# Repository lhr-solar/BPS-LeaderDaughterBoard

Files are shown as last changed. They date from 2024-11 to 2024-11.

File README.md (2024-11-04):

# BPS-LeaderDaughterBoard

The BPS Leader-Daughter is a daugherboard for the LeaderSOM. Together they will read data from and control the BPS peripherals

## Switches LEDs
| # | Purpose |
| - | - |
| D1  | Strobe Light Indicator |
| D3  | HV+ Contactor Indicator |
| D6  | HV- Contactor Indicator |
| D9  | Array Contactor Indicator |

[**BOM**](BOM/BPS-LeaderDaughterBOM.xls)  
[**IBOM**](BOM/ibom.html)  
[**Partial Mouser Cart**](https://www.mouser.com/ProjectManager/ProjectDetail.aspx?AccessID=2f994263ce7)  
[**All Components Mouser Cart**](https://www.mouser.com/ProjectManager/ProjectDetail.aspx?AccessID=f3b4372aef)  

## PCB


## Schematic
[**PDF with all sheets**](BPS-LeaderDaughterSchematic.pdf)

## Links
[Gigavac Contactor Circuit PWM Application Note](https://sensata.com/sites/default/files/a/Sensata-gigavac-driving-contactors-with-external-pwm-app-note.pdf)  
[Texas Instruments note on driving Contactors](https://www.ti.com/lit/wp/slvaf35/slvaf35.pdf?ts=1699022514322&ref_url=https%253A%252F%252Fwww.google.com%252F)

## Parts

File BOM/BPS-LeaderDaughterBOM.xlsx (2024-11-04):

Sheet: Full BOM
Reference | Value | Footprint | P/N | Qty
C1 | 1uF | Capacitor_SMD:C_0805_2012Metric | C0805C105K5PACTU | 1
D1, D3, D6, D9 | Green | LED_SMD:LED_0805_2012Metric_Pad1.15x1.40mm_HandSolder | APTD2012LCGCK | 4
D2, D5, D8 | BAS70-04 | Package_TO_SOT_SMD:SOT-23 | BAS70-04 | 3
D4, D7, D10, D11, D13, D15, D17 | 1N4448W | Diode_SMD:D_SOD-123 | 1N4448W | 7
D12, D14, D16, D18 | 3.3V | Diode_SMD:D_SOD-323 | BZT52B3V3 | 4
IC1 | ADT7470ARQZ-REEL7 | Package_SO:QSOP-16_3.9x4.9mm_P0.635mm | ADT7470 | 1
J1, J2 | DaughterConnector | UTSVT_Connectors:Molex_53307-2071 | 53307-2071 | 2
J3 | ErrorLightConn | UTSVT_Connectors:Molex_MicroFit3.0_1x2xP3.00mm_PolarizingPeg_Vertical | 43650-0215 | 1
J4-J7, J9-J12 | Conn_01x04 | UTSVT_Connectors:Molex_MicroFit3.0_1x4xP3.00mm_PolarizingPeg_Vertical | 436500244 | 8
J8 | Conn_01x03 | Connector_Molex:Molex_Micro-Fit_3.0_43650-0315_1x03_P3.00mm_Vertical | 436500315 | 1
Q1-Q8 | BUK9M23-80E | Package_TO_SOT_SMD:LFPAK33 | BUK9M23-80E | 8
R1, R5, R9, R13 | 1k | Resistor_SMD:R_0805_2012Metric | CRCW08051K00FKEAC | 4
R2, R7, R11, R15, R22, R24, R27, R29, R32, R34, R37, R39 | 10k | Resistor_SMD:R_0805_2012Metric | CRCW080510K0FKEAC | 12
R3, R6, R10, R14, R16, R18, R20, R21, R25, R26, R30, R31, R35, R36 | 100k | Resistor_SMD:R_0805_2012Metric | CRCW0805100KFKEAC | 14
R17, R19 | 600 | Resistor_SMD:R_0805_2012Metric | CRCW0805600RFKEAHP | 2
R23, R28, R33, R38 | 20k | Resistor_SMD:R_0805_2012Metric | CRCW080522K1FKEA | 4
U1, U2 | EL3H7 | Package_SO:SOP-4_4.4x2.6mm_P1.27mm | EL3H7(D)(TA)-VG | 2

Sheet: BOM to Order
Reference | Value | Footprint | P/N | Qty
D2, D5, D8 | BAS70-04 | Package_TO_SOT_SMD:SOT-23 | BAS70-04 | 3
D4, D7, D10, D11, D13, D15, D17 | 1N4448W | Diode_SMD:D_SOD-123 | 1N4448W | 7
D12, D14, D16, D18 | 3.3V | Diode_SMD:D_SOD-323 | BZT52B3V3 | 4
IC1 | ADT7470ARQZ-REEL7 | Package_SO:QSOP-16_3.9x4.9mm_P0.635mm | ADT7470 | 1
J1, J2 | DaughterConnector | UTSVT_Connectors:Molex_53307-2071 | 53307-2071 | 2
J3 | ErrorLightConn | UTSVT_Connectors:Molex_MicroFit3.0_1x2xP3.00mm_PolarizingPeg_Vertical | 43650-0215 | 1
Q1-Q8 | BUK9M23-80E | Package_TO_SOT_SMD:LFPAK33 | BUK9M23-80E | 8
R3, R6, R10, R14, R16, R18, R20, R21, R25, R26, R30, R31, R35, R36 | 100k | Resistor_SMD:R_0805_2012Metric | CRCW0805100KFKEAC | 14
R17, R19 | 600 | Resistor_SMD:R_0805_2012Metric | CRCW0805600RFKEAHP | 2
R23, R28, R33, R38 | 20k | Resistor_SMD:R_0805_2012Metric | CRCW080522K1FKEA | 4
U1, U2 | EL3H7 | Package_SO:SOP-4_4.4x2.6mm_P1.27mm | EL3H7(D)(TA)-VG | 2

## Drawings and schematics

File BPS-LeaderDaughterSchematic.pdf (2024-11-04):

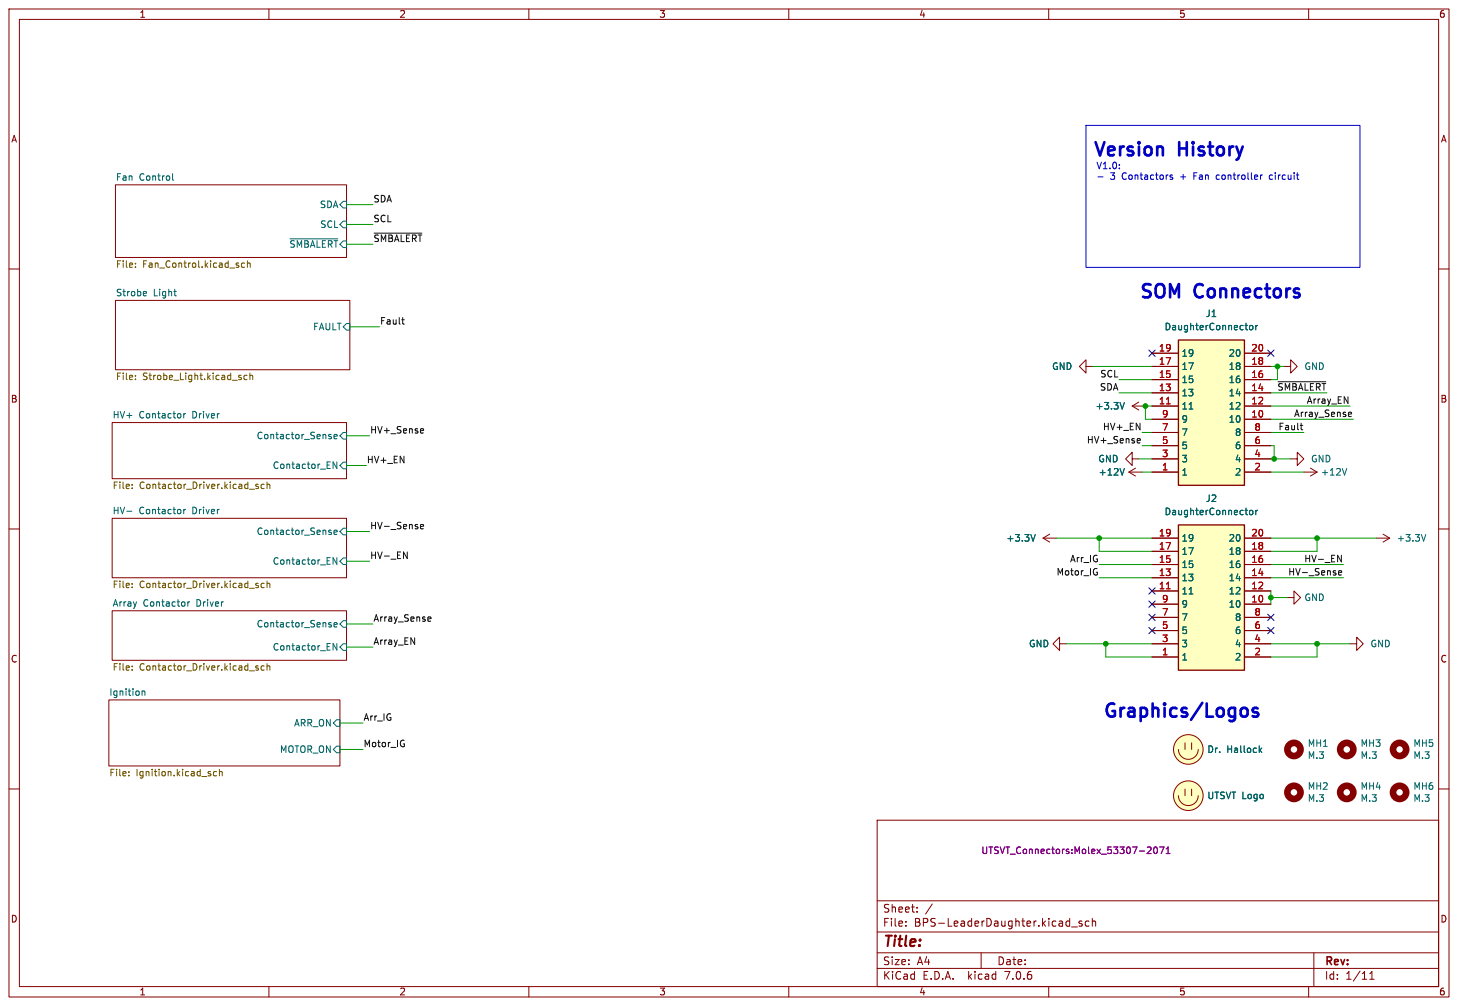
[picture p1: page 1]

Id: 1/11 Title: File: BPS-LeaderDaughter.kicad_sch Sheet: /

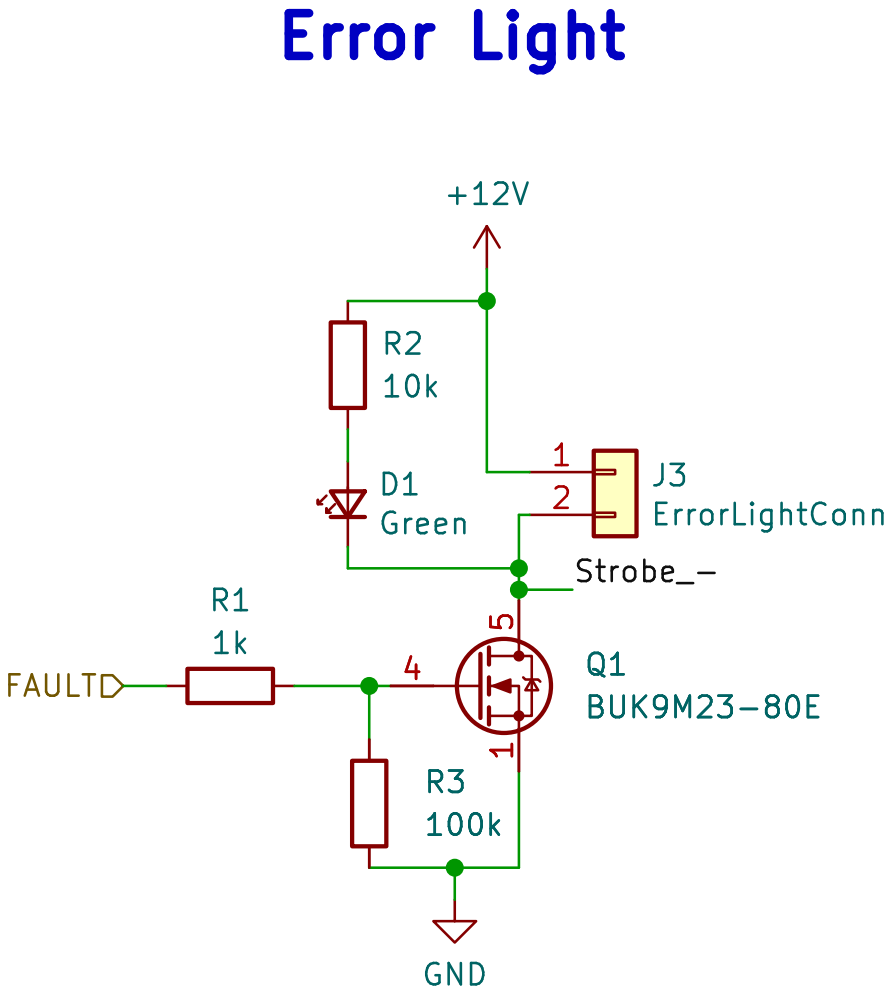
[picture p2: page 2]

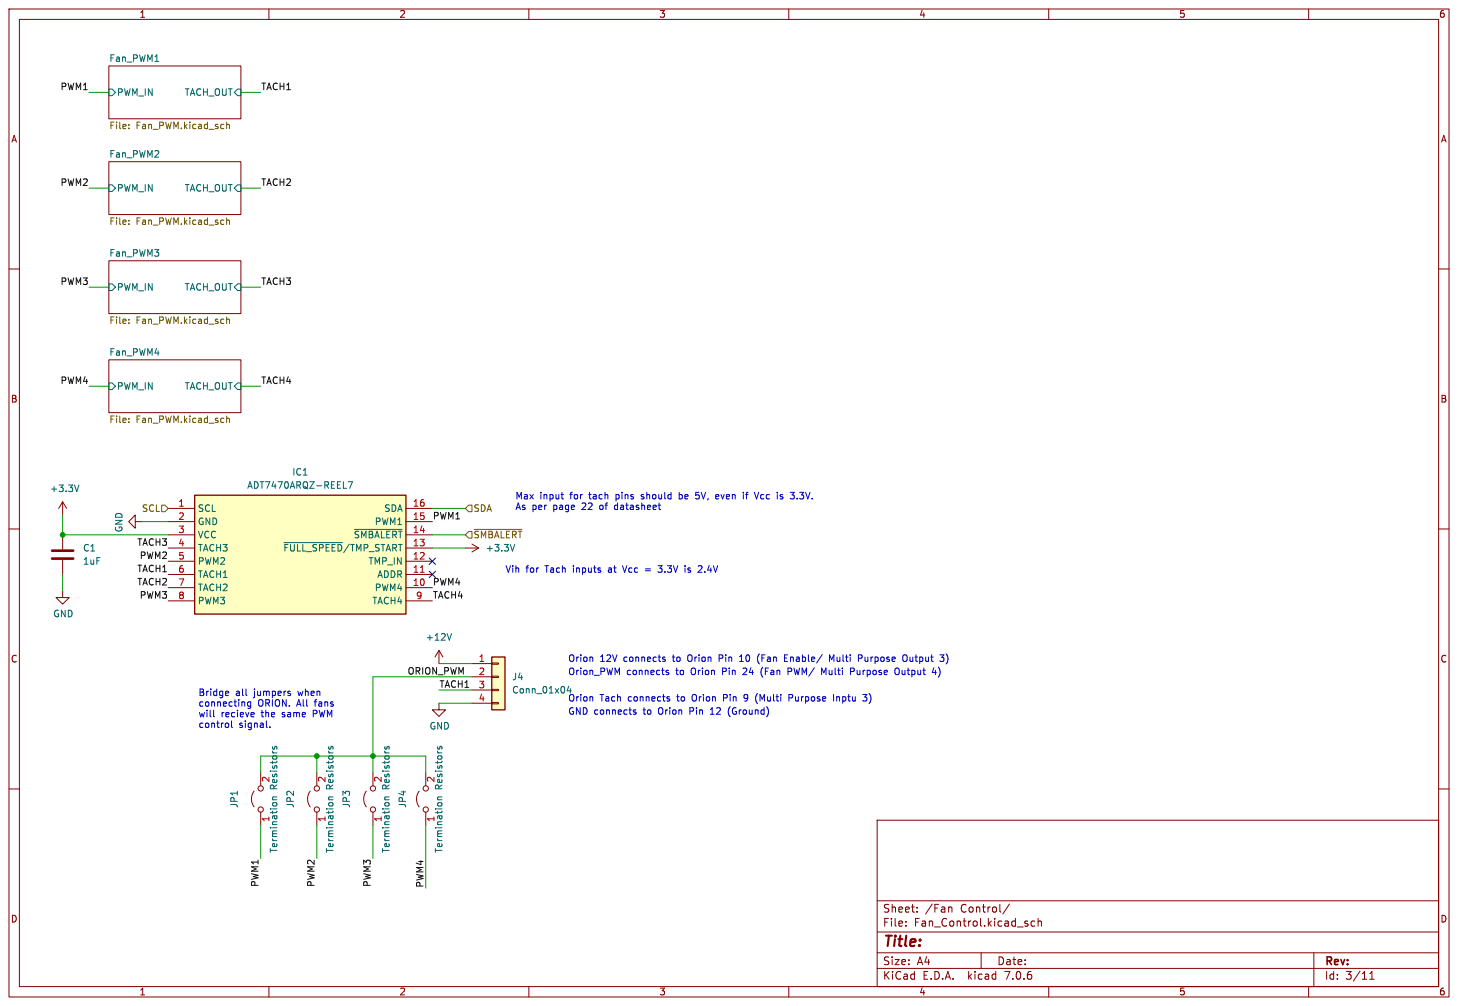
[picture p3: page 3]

1 2 JP4 Termination Resistors 1 2 JP3 Termination Resistors C1

Bridge all jumpers when

Id: 3/11 Title: File: Fan_Control.kicad_sch Sheet: /Fan Control/

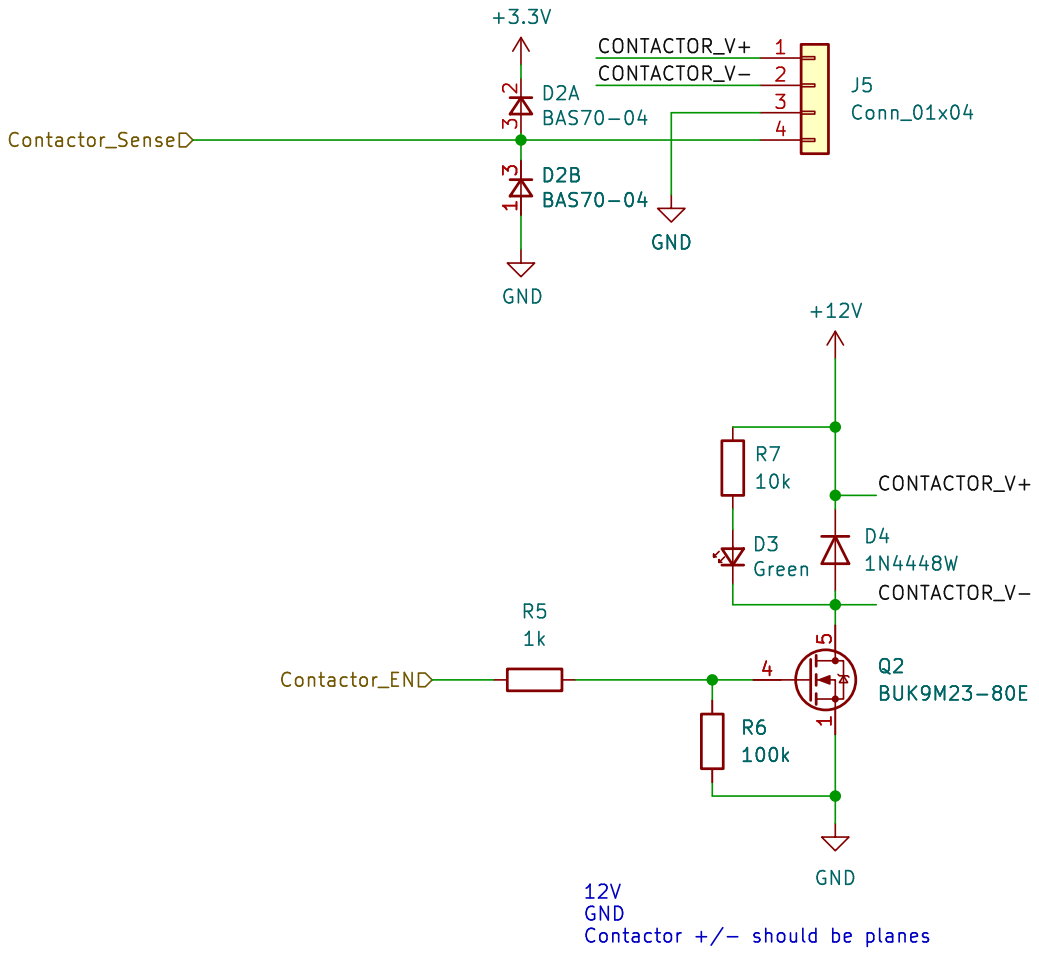
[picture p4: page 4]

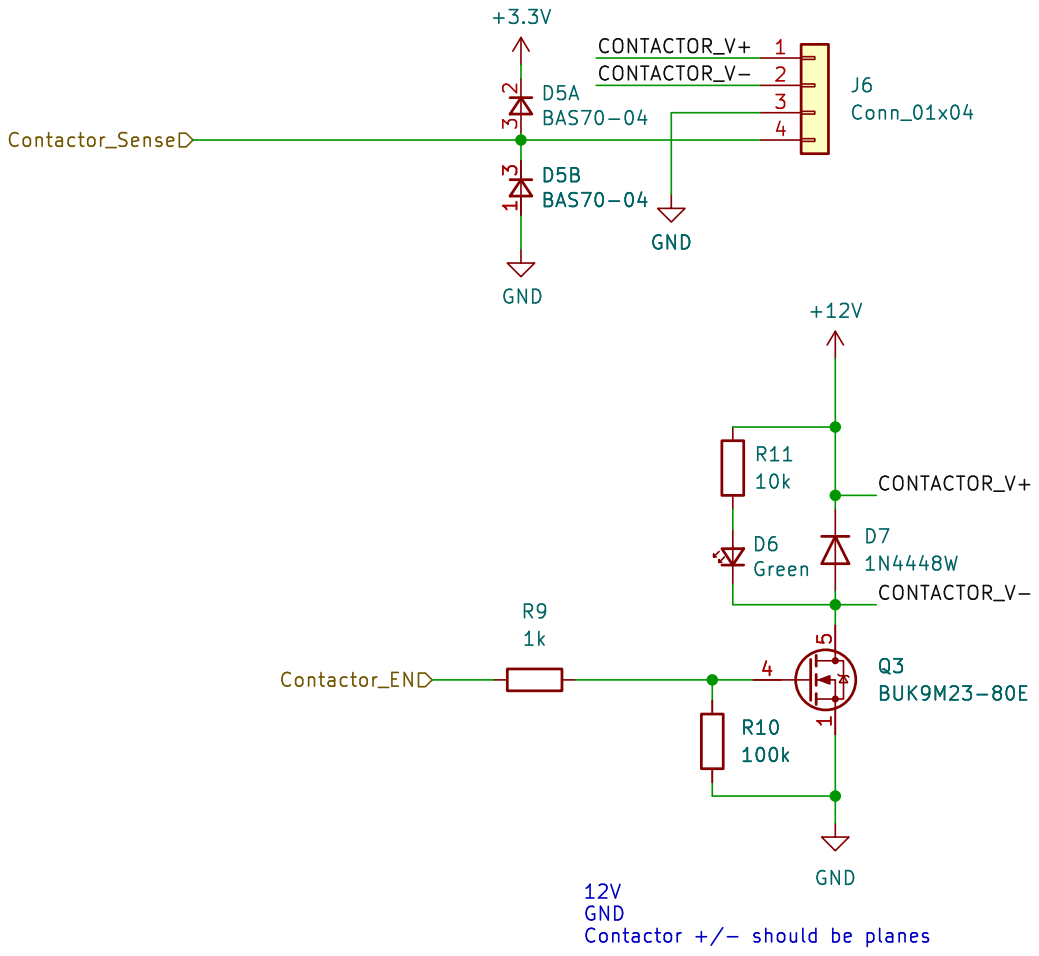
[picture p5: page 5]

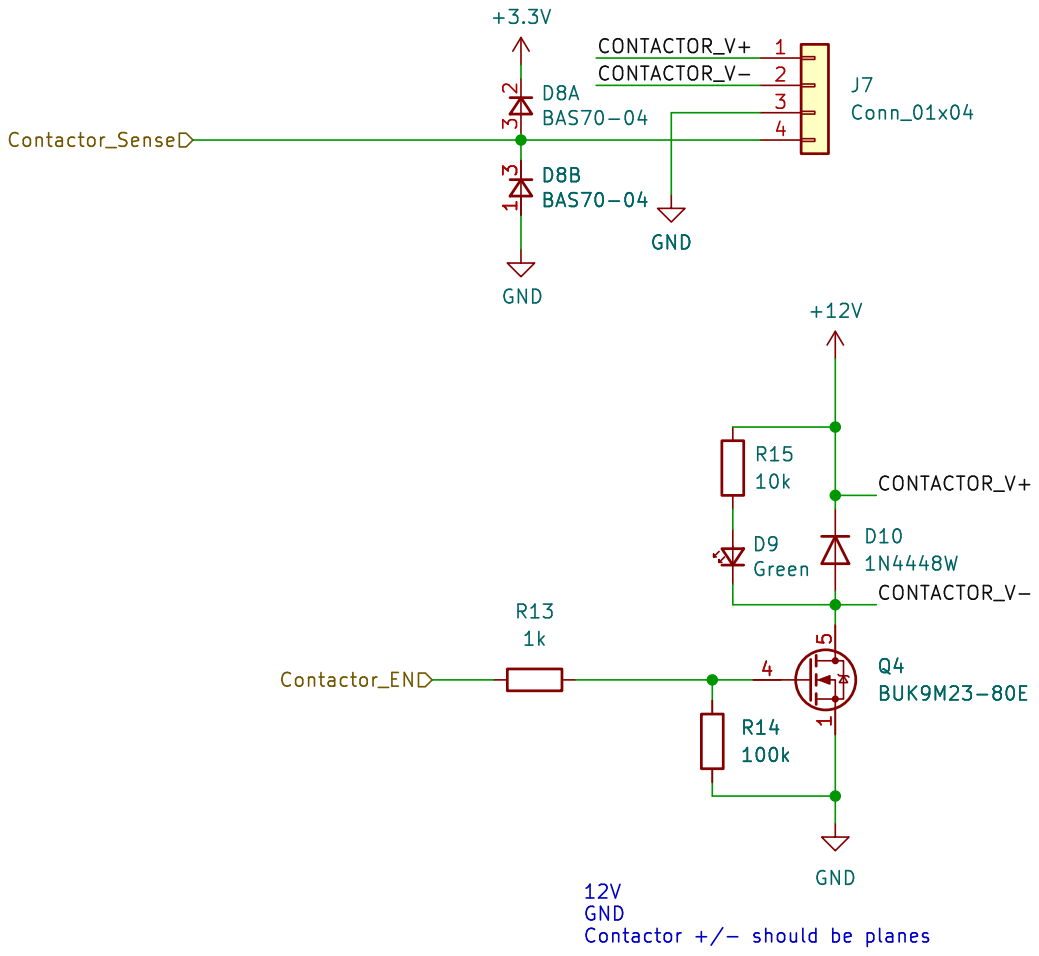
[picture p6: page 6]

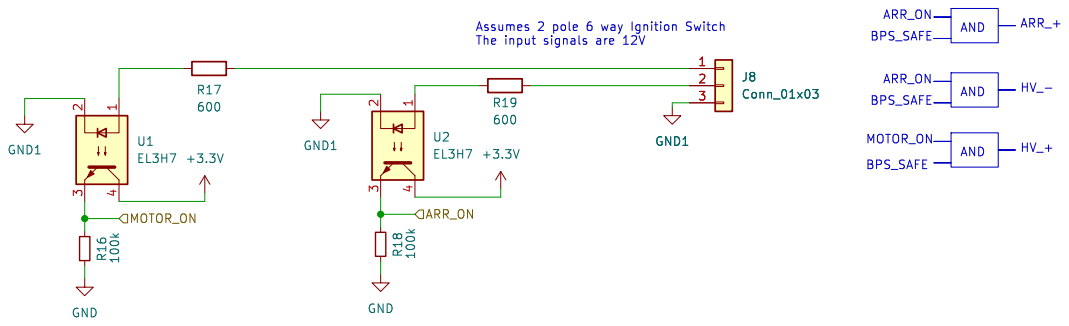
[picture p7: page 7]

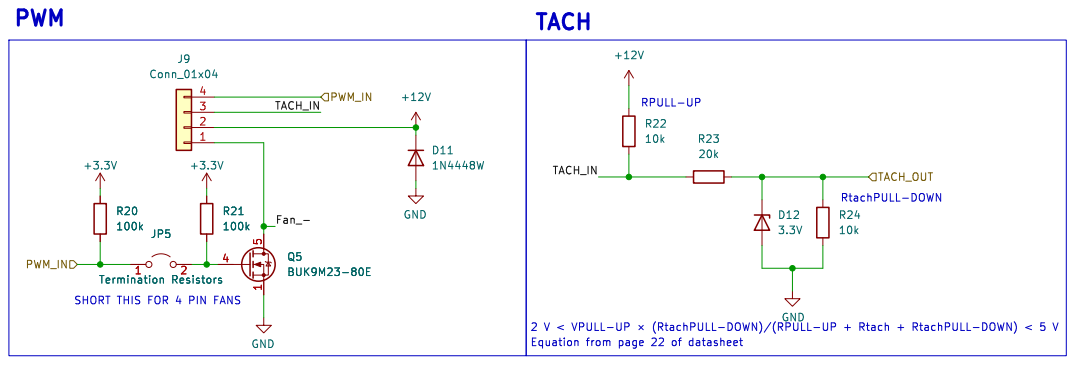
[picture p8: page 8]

SHORT THIS FOR 4 PIN FANS R20

Id: 8/11 Title: File: Fan_PWM.kicad_sch Sheet: /Fan Control/Fan_PWM1/

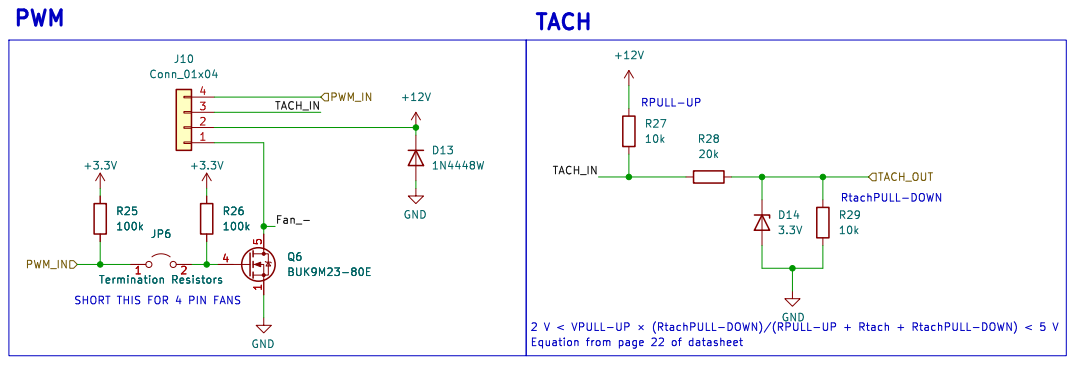
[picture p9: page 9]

SHORT THIS FOR 4 PIN FANS R26

Id: 9/11 Title: File: Fan_PWM.kicad_sch Sheet: /Fan Control/Fan_PWM2/

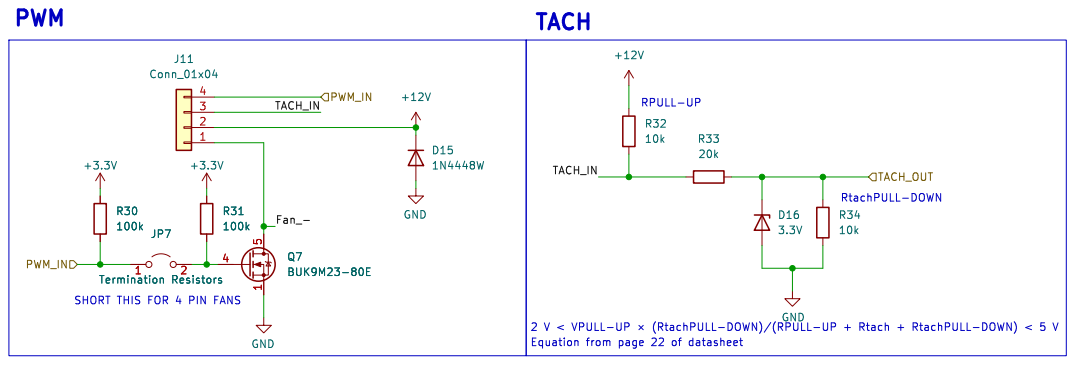
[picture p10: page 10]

SHORT THIS FOR 4 PIN FANS R30

Id: 10/11 Title: File: Fan_PWM.kicad_sch Sheet: /Fan Control/Fan_PWM3/

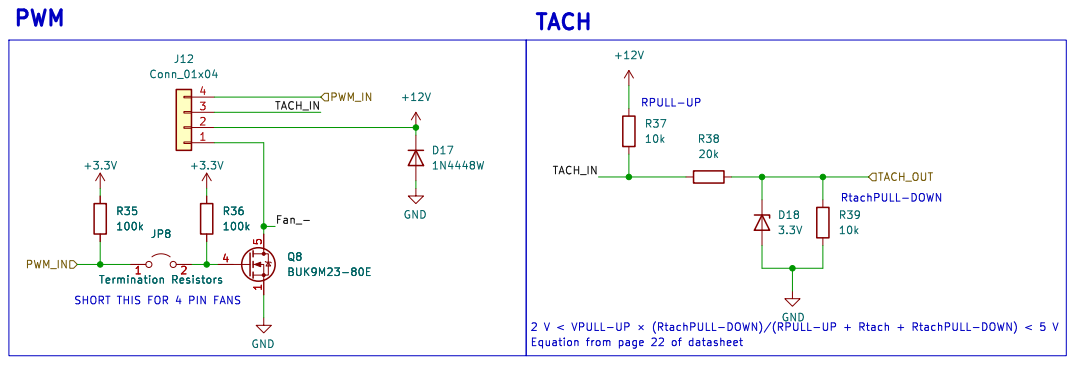
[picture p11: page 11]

SHORT THIS FOR 4 PIN FANS R35

Id: 11/11 Title: File: Fan_PWM.kicad_sch Sheet: /Fan Control/Fan_PWM4/

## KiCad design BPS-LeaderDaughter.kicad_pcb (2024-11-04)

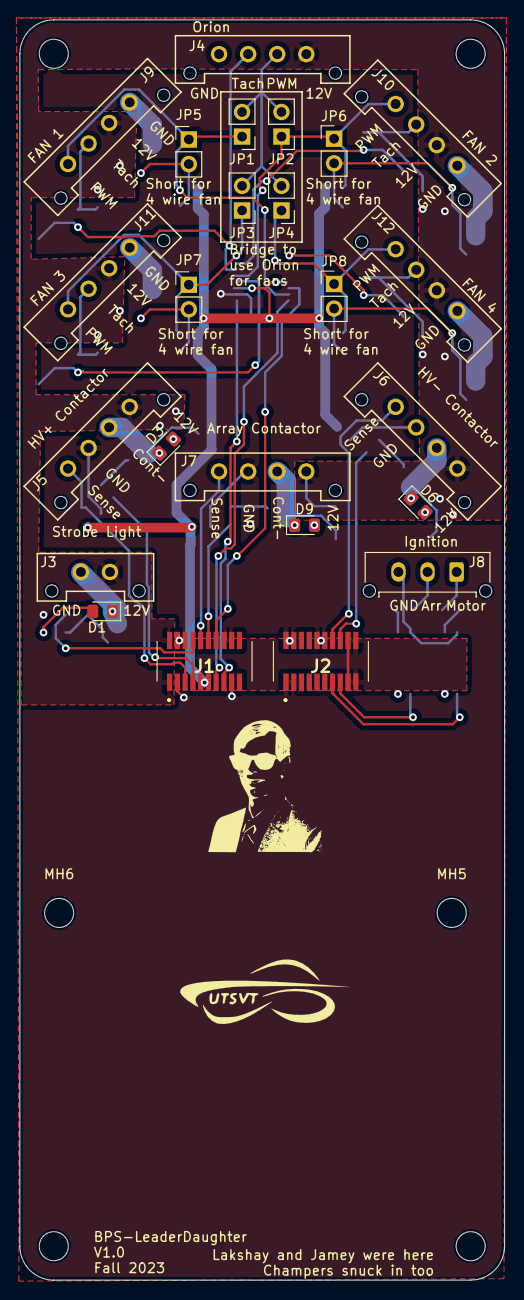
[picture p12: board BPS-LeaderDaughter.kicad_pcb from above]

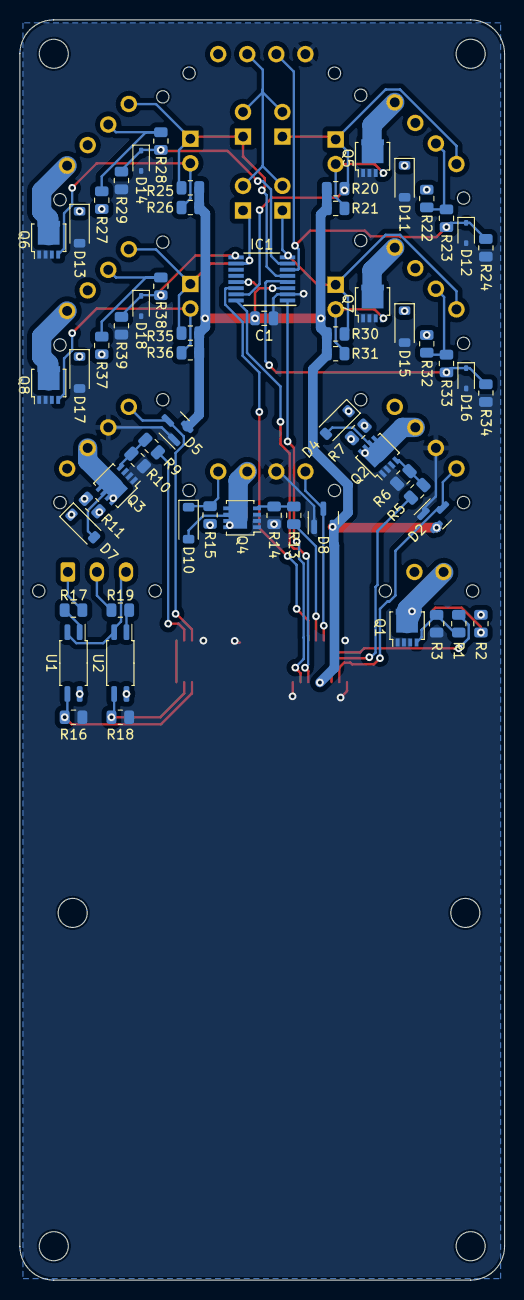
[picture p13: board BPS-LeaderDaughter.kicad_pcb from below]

Board: 2 copper layers, 50.0 x 130.0 mm, 94 parts (62 on the bottom side), 53 nets.

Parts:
C1: 1uF; C_0805_2012Metric
D1, D3, D6, D9: Green; LED_0805_2012Metric_Pad1.15x1.40mm_HandSolder
D2, D5, D8: BAS70-04; SOT-23
D4, D7, D10, D11, D13, D15, D17: 1N4448W; D_SOD-123
D12, D14, D16, D18: 3.3V; D_SOD-323
IC1: ADT7470ARQZ-REEL7; QSOP-16_3.9x4.9mm_P0.635mm
J1, J2: DaughterConnector; Molex_53307-2071
J3: ErrorLightConn; Molex_MicroFit3.0_1x2xP3.00mm_PolarizingPeg_Vertical
J4, J5, J6, J7, J9, J10, J11, J12: Conn_01x04; Molex_MicroFit3.0_1x4xP3.00mm_PolarizingPeg_Vertical
J8: Conn_01x03; Molex_Micro-Fit_3.0_43650-0315_1x03_P3.00mm_Vertical
JP1, JP2, JP3, JP4, JP5, JP6, JP7, JP8: Termination Resistors; PinHeader_1x02_P2.54mm_Vertical
LOGO1: Dr. Hallock; Hallock_Image_Tiny
LOGO2: UTSVT Logo; UTSVT_Logo_Symbol
MH1, MH2, MH3, MH4, MH5, MH6: M.3; MountingHole_3mm
Q1, Q2, Q3, Q4, Q5, Q6, Q7, Q8: BUK9M23-80E; LFPAK33
R1, R5, R9, R13: 1k; R_0805_2012Metric
R2, R7, R11, R15, R22, R24, R27, R29, R32, R34, R37, R39: 10k; R_0805_2012Metric
R3, R6, R10, R14, R16, R18, R20, R21, R25, R26, R30, R31, R35, R36: 100k; R_0805_2012Metric
R17, R19: 600; R_0805_2012Metric
R23, R28, R33, R38: 20k; R_0805_2012Metric
U1, U2: EL3H7; SOP-4_4.4x2.6mm_P1.27mm

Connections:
+3.3V: C1.1, D2.2, D5.2, D8.2, IC1.3 (VCC), IC1.13 (~FULL_SPEED/TMP_START), J1.9, J1.11, J2.17, J2.18, J2.19, J2.20, R20.1, R21.1, R25.1, R26.1, R30.1, R31.1, R35.1, R36.1, U1.4, U2.4
+12V: D4.1 (K), D7.1 (K), D10.1 (K), D11.1 (K), D13.1 (K), D15.1 (K), D17.1 (K), J1.1, J1.2, J3.1, J4.1, J5.1, J6.1, J7.1, J9.2, J10.2, J11.2, J12.2, R2.1, R7.1, R11.1, R15.1, R22.1, R27.1, R32.1, R37.1
/Arr_IG: J2.15, R18.2, U2.3
/Array Contactor Driver/CONTACTOR_V-: D9.1 (K), D10.2 (A), J7.2, Q4.5 (D)
/Array_EN: J1.12, R13.1
/Array_Sense: D8.3, J1.10, J7.4
/Fan Control/Fan_PWM1/Fan_-: J9.1, Q5.5 (D)
/Fan Control/Fan_PWM1/TACH_IN: J9.3, R22.2, R23.1
/Fan Control/Fan_PWM2/Fan_-: J10.1, Q6.5 (D)
/Fan Control/Fan_PWM2/TACH_IN: J10.3, R27.2, R28.1
/Fan Control/Fan_PWM3/Fan_-: J11.1, Q7.5 (D)
/Fan Control/Fan_PWM3/TACH_IN: J11.3, R32.2, R33.1
/Fan Control/Fan_PWM4/Fan_-: J12.1, Q8.5 (D)
/Fan Control/Fan_PWM4/TACH_IN: J12.3, R37.2, R38.1
/Fan Control/ORION_PWM: J4.2, JP1.2 (B), JP2.2 (B), JP3.2 (B), JP4.2 (B)
/Fan Control/PWM1: IC1.15 (PWM1), J9.4, JP1.1 (A), JP5.1 (A), R20.2
/Fan Control/PWM2: IC1.5 (PWM2), J10.4, JP2.1 (A), JP6.1 (A), R25.2
/Fan Control/PWM3: IC1.8 (PWM3), J11.4, JP3.1 (A), JP7.1 (A), R30.2
/Fan Control/PWM4: IC1.10 (PWM4), J12.4, JP4.1 (A), JP8.1 (A), R35.2
/Fan Control/TACH1: D12.1 (K), IC1.6 (TACH1), J4.3, R23.2, R24.1
/Fan Control/TACH2: D14.1 (K), IC1.7 (TACH2), R28.2, R29.1
/Fan Control/TACH3: D16.1 (K), IC1.4 (TACH3), R33.2, R34.1
/Fan Control/TACH4: D18.1 (K), IC1.9 (TACH4), R38.2, R39.1
/Fault: J1.8, R1.1
/HV+ Contactor Driver/CONTACTOR_V-: D3.1 (K), D4.2 (A), J5.2, Q2.5 (D)
/HV+_EN: J1.7, R5.1
/HV+_Sense: D2.3, J1.5, J5.4
/HV- Contactor Driver/CONTACTOR_V-: D6.1 (K), D7.2 (A), J6.2, Q3.5 (D)
/HV-_EN: J2.16, R9.1
/HV-_Sense: D5.3, J2.14, J6.4
/Motor_IG: J2.13, R16.2, U1.3
/SCL: IC1.1 (SCL), J1.15
/SDA: IC1.16 (SDA), J1.13
/Strobe Light/Strobe_-: D1.1 (K), J3.2, Q1.5 (D)
/~SMBALERT: IC1.14 (~SMBALERT), J1.14
GND: C1.2, D2.1, D5.1, D8.1, D11.2 (A), D12.2 (A), D13.2 (A), D14.2 (A), D15.2 (A), D16.2 (A), D17.2 (A), D18.2 (A), IC1.2 (GND), J1.3, J1.4, J1.6, J1.16, J1.17, J1.18, J2.1, J2.2, J2.3, J2.4, J2.10, J2.12, J4.4, J5.3, J6.3, J7.3, Q1.1 (S), Q1.2 (S), Q1.3 (S), Q2.1 (S), Q2.2 (S), Q2.3 (S), Q3.1 (S), Q3.2 (S), Q3.3 (S), Q4.1 (S), Q4.2 (S), Q4.3 (S), Q5.1 (S), Q5.2 (S), Q5.3 (S), Q6.1 (S), Q6.2 (S), Q6.3 (S), Q7.1 (S), Q7.2 (S), Q7.3 (S), Q8.1 (S), Q8.2 (S), Q8.3 (S), R3.2, R6.2, R10.2, R14.2, R16.1, R18.1, R24.2, R29.2, R34.2, R39.2
GND1: J8.3, U1.2, U2.2
unnamed: D1.2 (A), R2.2
unnamed: D3.2 (A), R7.2
unnamed: D6.2 (A), R11.2
unnamed: D9.2 (A), R15.2
unnamed: J8.1, R17.2
unnamed: J8.2, R19.2
unnamed: JP5.2 (B), Q5.4 (G), R21.2
unnamed: JP6.2 (B), Q6.4 (G), R26.2
unnamed: JP7.2 (B), Q7.4 (G), R31.2
unnamed: JP8.2 (B), Q8.4 (G), R36.2
unnamed: Q1.4 (G), R1.2, R3.1
unnamed: Q2.4 (G), R5.2, R6.1
unnamed: Q3.4 (G), R9.2, R10.1
unnamed: Q4.4 (G), R13.2, R14.1
unnamed: R17.1, U1.1
unnamed: R19.1, U2.1

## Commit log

2023-09-23 intial KiCAD settup
    [BPS-LeaderDaughter.kicad_pcb, BPS-LeaderDaughter.kicad_sch]
2023-09-23 Added strobe light + Som Connectors
    [BPS-LeaderDaughter.kicad_sch, Strobe_Light.kicad_sch]
2024-11-04 V1.0 - PCB (#2)
    * Add new branch
    * added fan control heirarchical sheet
    * Standardized strobe liight
    * Added Contactor Driver circuit
    * Added more documentatino to the Contactor circuits
    * Added part numbers and datasheet to isolator part
    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
    [BPS-LeaderDaughter-B_Cu.gbr, BPS-LeaderDaughter-B_Mask.gbr, BPS-LeaderDaughter-B_Paste.gbr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]
